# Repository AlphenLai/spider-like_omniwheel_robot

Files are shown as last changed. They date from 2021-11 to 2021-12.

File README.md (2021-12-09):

# spider-like_omniwheel_robot

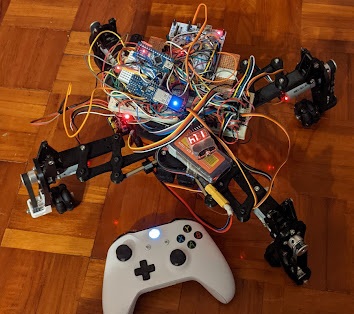
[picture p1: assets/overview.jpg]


This is a robot inspired by [Tachikoma](https://ghostintheshell.fandom.com/wiki/Tachikoma) from Ghost in the Shell. A robot with wheeled legs which allows it to switch between quadruped mode and vehicle mode.

This project was barely finished under a lot of compromise, due to series of inappropriate selection on software development platform and overthinking mechanical design. The robot is only capable in variable wheel angles by moving the position of its legs. Quadruped mode and other planned features are never implemented because of foreseeably  time-consuming efforts needed for completion.

## Hardware

### MCU

stm32f103rb nucleo

### Power Supply

MP1584EN DC-DC voltage regulator module (3A)

### Servo

MG995 servo (180 degree) x4

> note: 3A power supply is not enough to driver servo against any torque (eg: friction from ground). Continuing driving them will cause system blackout.

### Remote control

https://github.com/AlphenLai/arduino_nano_usb_host_shield

### Motor drivers

[TB6612FNG](https://www.sparkfun.com/datasheets/Robotics/TB6612FNG Breakout v11.zip) x2

### Motors 

25GA370 x4

280rpm, 12V

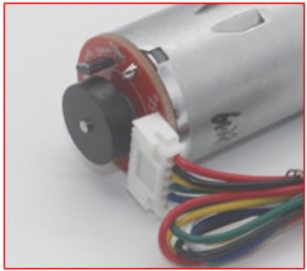
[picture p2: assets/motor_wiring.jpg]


| Colour | definition |
| --- | --- |
| Red | Motor + |
| Black  | Encoder -  |
| Yellow | Encoder A  |
| Green  | Encoder B  |
| Blue | Encoder +  |
| White  | Motor - |

### Wheel

1.5 inch omni wheel

### Chassis

[3D printed](./3D_printe_parts/)

Considered ease of program in omniwheel mode, and early planned "variable wheel angle", the legs are designed as concentric. This guarantee wheels being aligned to the centre as wherever the legs move, but also requires complicated mechanical design. This decision also scarified structural stability.

### Wiring



## Software

### OS

mbed-os. Unfortunately mbed-os is not designed for RTOS. It took a lot of efforts to implement the robot into the system.

| Module | Usage |
| --- | --- |
| config | Set pinout and global variables |
| controller | Handles controller signals (from serial) |
| encoder | Handles encoder feedbacks (signals proven to be delayed)  (discontinued) |
| extended_servo | Break servo movements by parts to create smooth transitions (discontinued) |
| hardware_io | Handles physical inputs such as buttons/potentiometer |
| **main** | Program entry point. Registers modules as threads |
| math_alg | Provide algorithm computation service (discontinued) |
| motion_control | Handles path following (discontinued) |
| motor_control  | Handles control signals to motor controller board |
| pid | Provide PID computation service (discontinued) |
| placeholder | Plain files for creating new module in mbed web compiler |
| serial | Handles serial traffic |
| servo_control  | Handles servo movements |
| usb_interface  | Handles usb interface in serial0/serial_pc. Receiver control signals from USB serial line. |

### Algorithm

#### Equation to drive a 4 wheels omniwheel robot



where 
R = radius of robot from body centre to wheel centre
r = radius of wheel
w = angular velocity of wheel
theta = body rotation (angle degree)
alpha = angle of wheel from centre of robot (assume the shaft points to centre of robot)
Vx = x axis velocity of robot
Vy = y axis velocity of robot
dot theta = angular velocity of robot (anti-clockwise)

To convert global frame to local frame (relative to robot body), multiple by the following matrix:



Compute the equation above will get the equation for each wheel:

**global frame**



**local frame**



For this robot, motors are ordered by body frame.

But their angles are assigned from 12 o'clock in clockwise due to the ease of following references in early stage.



## Demo

Watch the video (https://youtu.be/Zyg-uMiATHM)

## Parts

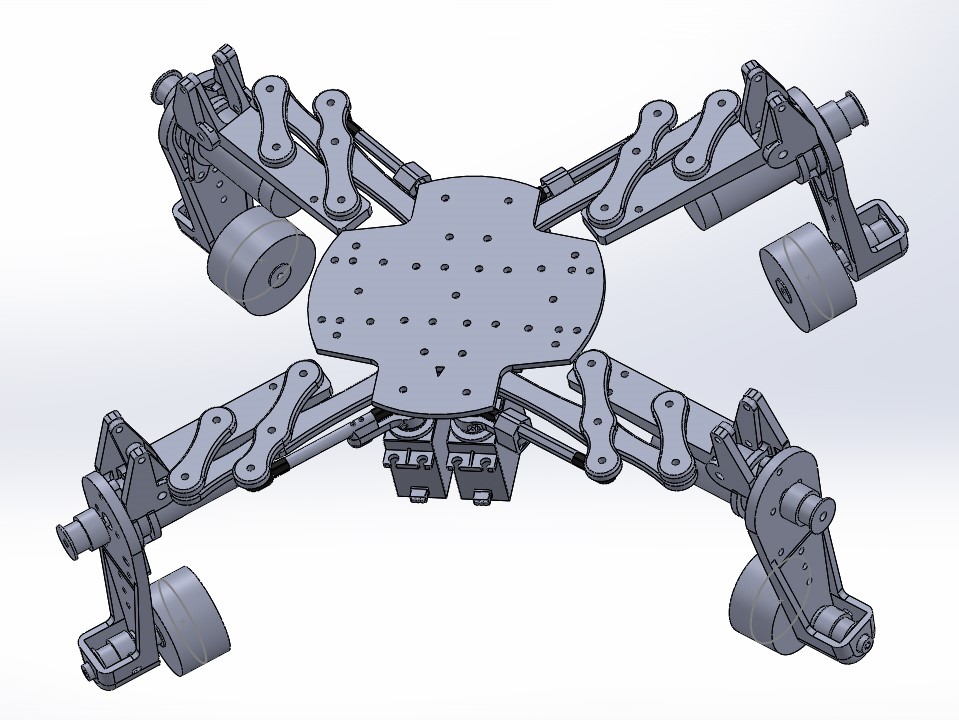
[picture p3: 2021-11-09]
3D_printed_parts/preview.JPG

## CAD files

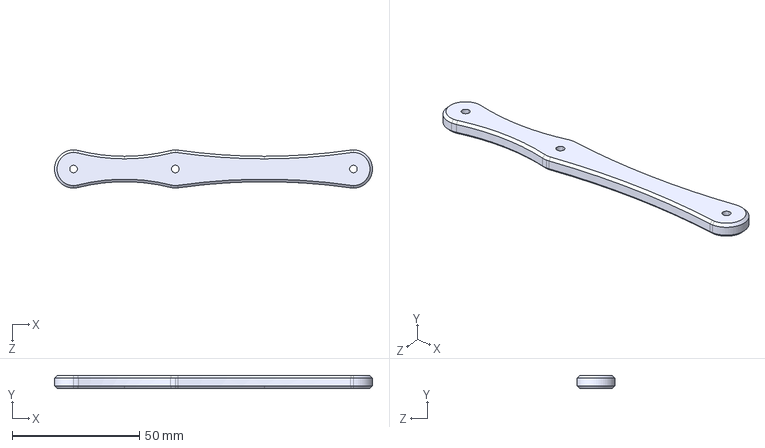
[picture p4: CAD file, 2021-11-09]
3D_printed_parts/x4_3dp_coxa_mainshaft.STEP
125.0 x 5.00 x 15.0 mm

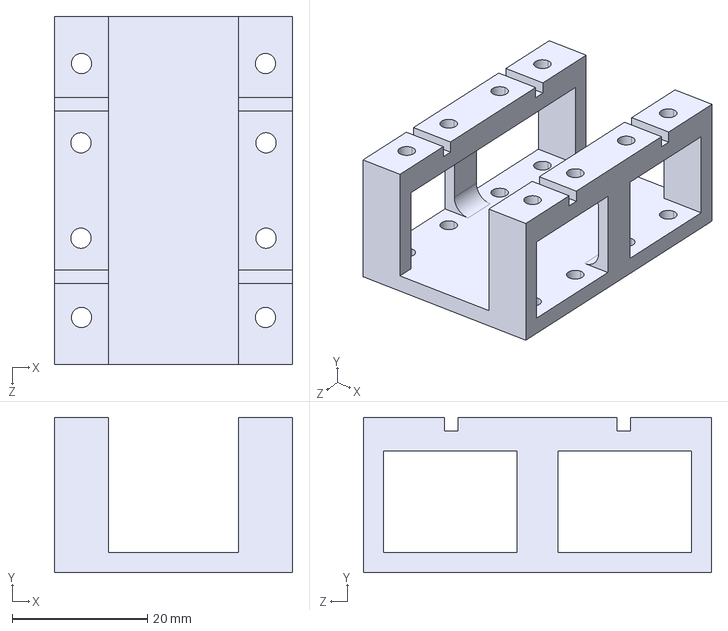
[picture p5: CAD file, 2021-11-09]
3D_printed_parts/x1_3DP_servo_mount_under_main.STEP
35.2 x 23.0 x 51.6 mm

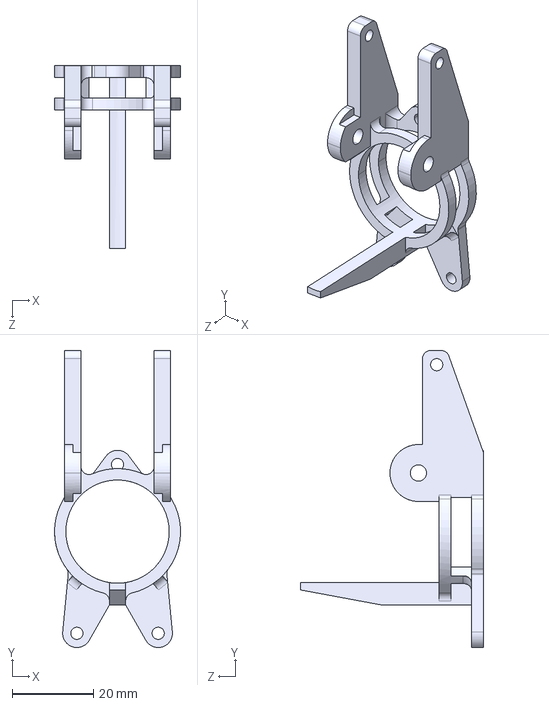
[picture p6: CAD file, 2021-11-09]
3D_printed_parts/x4_3dp_femur-leg.STEP
31.0 x 73.0 x 45.0 mm

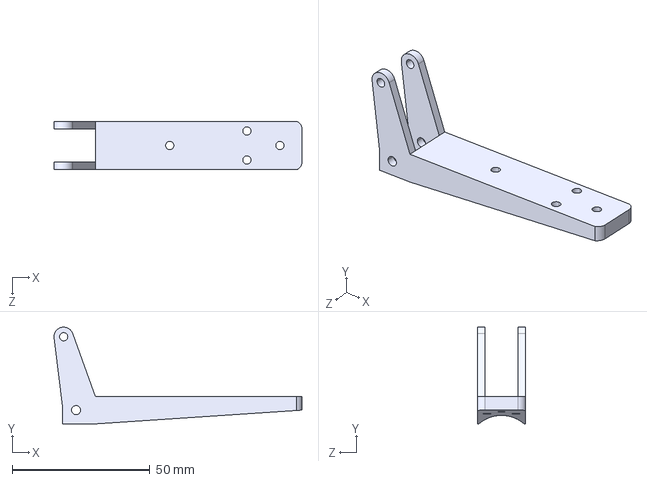
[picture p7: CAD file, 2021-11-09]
3D_printed_parts/x4_3dp_femur-fix.STEP
90.0 x 35.1 x 17.6 mm

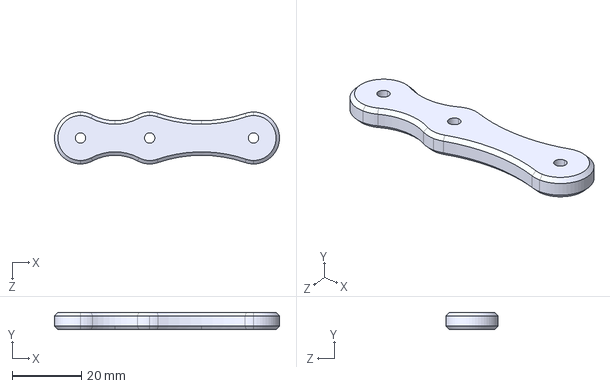
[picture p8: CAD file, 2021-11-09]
3D_printed_parts/x4_3dp_coxa_cross.STEP
65.0 x 5.00 x 15.0 mm

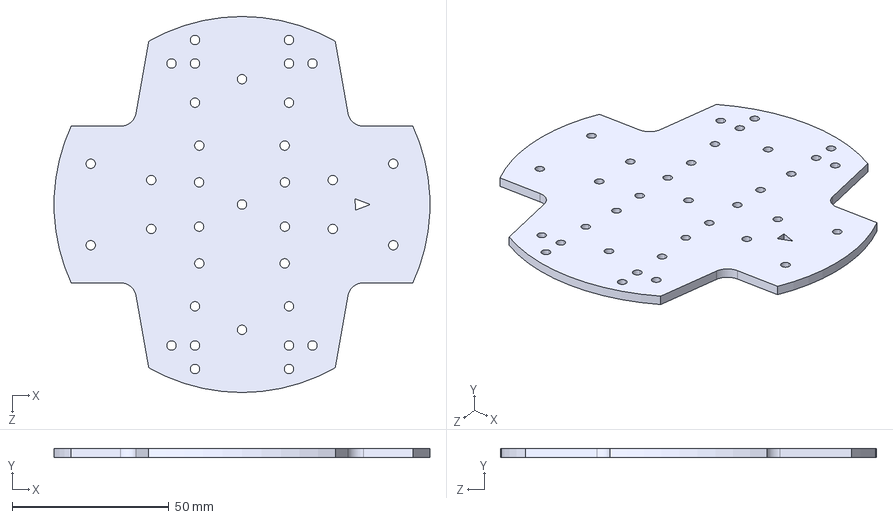
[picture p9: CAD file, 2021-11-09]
3D_printed_parts/x1_3dp_LC_body.STEP
119.9 x 3.00 x 120.0 mm

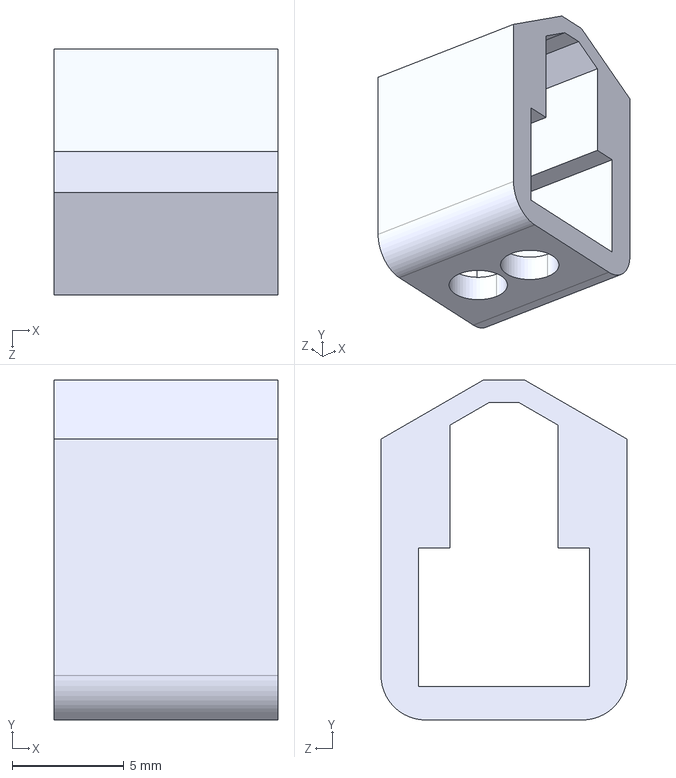
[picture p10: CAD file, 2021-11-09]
3D_printed_parts/x4_3dp_pillar_sheeve.STEP
10.0 x 15.2 x 11.0 mm

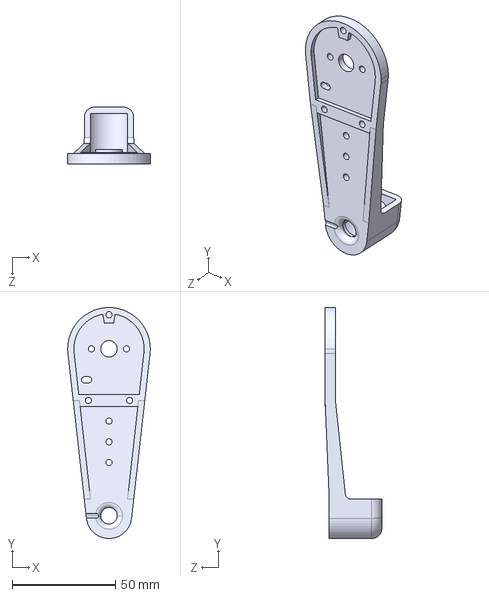
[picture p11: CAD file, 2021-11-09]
3D_printed_parts/x4_3dp_leg_proto_alt.STEP
40.0 x 111.8 x 27.5 mm

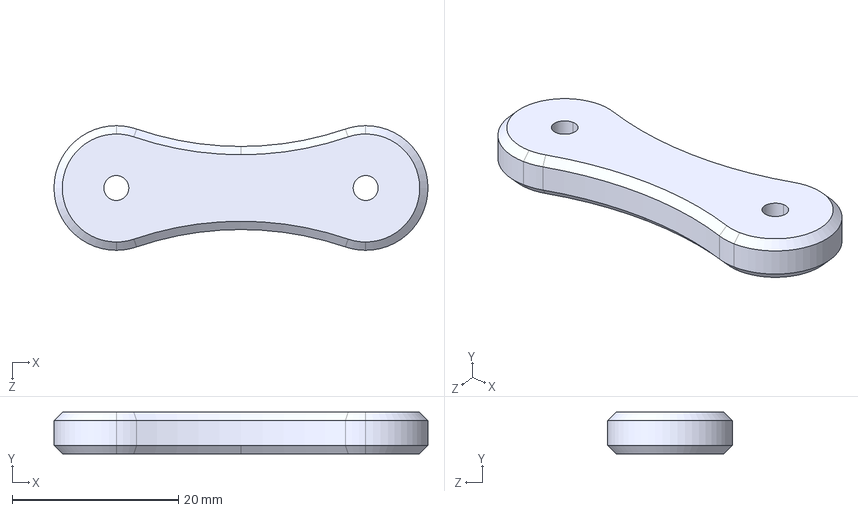
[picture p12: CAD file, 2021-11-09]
3D_printed_parts/x4_3dp_coxa_endshaft.STEP
45.0 x 5.00 x 15.0 mm

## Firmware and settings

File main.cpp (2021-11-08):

#include "mbed.h"
#include "config.h"
#include "serial.h"
#include "servo_control.h"
#include "hardware_io.h"
#include "motor_control.h"
#include "encoder.h"
#include "motion_control.h"
#include "usb_interface.h"
#include "controller.h"

#define USE_CONSOLE true

//place this line to io thread cpp later
DigitalOut debug_led(LD2);
extern Timer t;
extern RawSerial pc;

extern float sys_v_x;
extern float sys_v_y;
extern float sys_v_theta;

void led_thread()
{
    while (true) {
        debug_led = !debug_led;
        wait(1);
    }
}

int main()
{
    //Thread thread1(osPriorityNormal, 0.5 * 1024);   //0.5 * 1k stacks
    Thread thread2(osPriorityNormal, 1 * 1024);
    Thread thread3(osPriorityNormal, 0.5 * 1024);
    Thread thread4(osPriorityNormal, 1 * 1024);
    //Thread thread5(osPriorityNormal, 0.5 * 1024);
    //Thread thread6(osPriorityNormal, 1 * 1024);
    //Thread thread7(osPriorityNormal, 1 * 1024);
    Thread thread8(osPriorityNormal, 1 * 1024);
    Thread thread9(osPriorityNormal, 0.5 * 1024);
    
    pc.printf("\n\n=== Omniwheel Robot Test Platform ===\n\r");
    pc.printf("                            --Unit 00 v0 mod 1\n\n\r");
    t.start();
    
    //thread1.start(led_thread);
    thread2.start(servo_control);
    thread3.start(hardware_io);    
    thread4.start(motor_control);
    //thread5.start(encoder);
    //thread6.start(motion_control);
    //thread7.start(usb_interface);
    thread8.start(controller);
    thread9.start(serial);
    
    while(1)
    {
        wait(30);
        char buffer[50] = "running\n\r";
        pc_print(buffer);
        
        /*
        sys_v_x = 0.0;
        sys_v_y = 0.0;
        sys_v_theta = 3.0;
        wait(1);
        */
    }
}

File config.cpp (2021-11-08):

#include "config.h"
#include "mbed.h"
#include "extended_servo.h"
#include "motor_control.h"
#include "QEI.h"
#include "serial.h"

Timer t;

bool ready_to_start = false;

RawSerial pc(USBTX, USBRX, 57600); // tx, rx
RawSerial nano(S1TX, PB_7, 57600);

Serial_buffer pc_serial;
Serial_buffer nano_serial;

//put in a struct next version
const char *VAR_TABLE[] = {
    "ready_to_start",
    "motor1",
    "motor2",
    "motor3",
    "motor4",
    "m1_speed",
    "m2_speed",
    "m3_speed",
    "m4_speed",
    "sys_v_x = 0",
    "sys_v_y = 0.5",
    "sys_v_theta = 0",
    "sys_x = 0",
    "sys_y = 0",
    "sys_theta = 0",
    "m1_encoder",
    "m2_encoder",
    "m3_encoder",
    "m4_encoder"
};

uint8_t var_table_len = sizeof(VAR_TABLE);
uint8_t var_table_ele = sizeof(VAR_TABLE[0]);

//hw var
float wheel_r = 0.019;
float chassis_R = 0.1453;
float motor1_pos = 45.0 * pi/180.0;
float motor2_pos = 315.0 * pi/180.0;
float motor3_pos = 225.0 * pi/180.0;
#if MOTOR_NUMBER == 4
float motor4_pos = 135.0 * pi/180.0;
#endif

//servo var
#if USE_SERVO1 == true
Servo servo1(SERVO1_PIN);
Extended_servo servo1_handler;
#endif

float servo1_init = 45.0;
float servo1_angle = servo1_init;
float servo1_angle_range = 90;
float servo1_max = 0.875;
float servo1_min = 0.47;

#if USE_SERVO2 == true
Servo servo2(SERVO2_PIN);
Extended_servo servo2_handler;
#endif

float servo2_init = 45;
float servo2_angle = servo2_init;
float servo2_angle_range = 90;
float servo2_max = 0.84;
float servo2_min = 0.415;

#if USE_SERVO3 == true
Servo servo3(SERVO3_PIN);
Extended_servo servo3_handler;
#endif

float servo3_init = 45;
float servo3_angle = servo3_init;
float servo3_angle_range = 90;
float servo3_max = 0.85;
float servo3_min = 0.445;

#if USE_SERVO4 == true
Servo servo4(SERVO4_PIN);
Extended_servo servo4_handler;
#endif

float servo4_init = 45;
float servo4_angle = servo4_init;
float servo4_angle_range = 90;
float servo4_max = 0.845;
float servo4_min = 0.44;
//---

//motor var
float max_speed = 0.25;
float min_speed = -1.0;
float sys_speed = 1.0;                  //speed of the whole system

PwmOut m1_pwm_out(MOTOR1_PWM_PIN);
PwmOut m2_pwm_out(MOTOR2_PWM_PIN);
PwmOut m3_pwm_out(MOTOR3_PWM_PIN);
#if MOTOR_NUMBER == 4
PwmOut m4_pwm_out(MOTOR4_PWM_PIN);
#endif

DigitalOut m1_in1_out(MOTOR1_IN1_PIN);
DigitalOut m1_in2_out(MOTOR1_IN2_PIN);
DigitalOut m2_in1_out(MOTOR2_IN1_PIN);
DigitalOut m2_in2_out(MOTOR2_IN2_PIN);
DigitalOut m3_in1_out(MOTOR3_IN1_PIN);
DigitalOut m3_in2_out(MOTOR3_IN2_PIN);
#if MOTOR_NUMBER == 4
DigitalOut m4_in1_out(MOTOR4_IN1_PIN);
DigitalOut m4_in2_out(MOTOR4_IN2_PIN);
#endif

float m1_speed;                         //speed of individual motor in rad/s
float m2_speed;                         //speed of individual motor in rad/s
float m3_speed;                         //speed of individual motor in rad/s
#if MOTOR_NUMBER == 4
float m4_speed;                         //speed of individual motor in rad/s
#endif
Motor_controller motor1(MOTOR1_HW_INV);
Motor_controller motor2(MOTOR2_HW_INV);
Motor_controller motor3(MOTOR3_HW_INV);
#if MOTOR_NUMBER == 4
Motor_controller motor4(MOTOR4_HW_INV);
#endif
//---

//system motion
float sys_v_x = 0;
float sys_v_y = 0;
float sys_v_theta = 5;

float sys_x = 0;
float sys_y = 0;
float sys_theta = 0;
//---

//encoder var
QEI m1_encoder(MOTOR1_ENC_A, MOTOR1_ENC_B, NC, 624);
QEI m2_encoder(MOTOR2_ENC_A, MOTOR2_ENC_B, NC, 624);
QEI m3_encoder(MOTOR3_ENC_A, MOTOR3_ENC_B, NC, 624);
#if MOTOR_NUMBER == 4
QEI m4_encoder(MOTOR4_ENC_A, MOTOR4_ENC_B, NC, 624);
#endif

float m1_enc = 0;
float m2_enc = 0;
float m3_enc = 0;
#if MOTOR_NUMBER == 4
float m4_enc = 0;
#endif

//enc angular velocity
float cyc_pulse = 440.0;

float enc_v_x = 0;
float enc_v_y = 0;
float enc_v_theta = 0;

//enc odom
float enc_x = 0;
float enc_y = 0;
float enc_theta = 0;
//---

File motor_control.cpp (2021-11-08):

#include "motor_control.h"
#include "mbed.h"
#include "config.h"
#include "serial.h"
#include "math_alg.h"
#include "pid.h"

extern bool ready_to_start;
extern RawSerial pc;
extern Serial_buffer pc_serial;

extern float wheel_r;
extern float chassis_R;

extern float motor1_pos;
extern float motor2_pos;
extern float motor3_pos;
#if MOTOR_NUMBER == 4
extern float motor4_pos;
#endif

extern float max_speed;
extern float min_speed;
extern float sys_speed;

extern Motor_controller motor1;
extern Motor_controller motor2;
extern Motor_controller motor3;
#if MOTOR_NUMBER == 4
extern Motor_controller motor4;
#endif

extern PwmOut m1_pwm_out;
extern PwmOut m2_pwm_out;
extern PwmOut m3_pwm_out;
#if MOTOR_NUMBER == 4
extern PwmOut m4_pwm_out;
#endif

extern DigitalOut m1_in1_out;
extern DigitalOut m1_in2_out;
extern DigitalOut m2_in1_out;
extern DigitalOut m2_in2_out;
extern DigitalOut m3_in1_out;
extern DigitalOut m3_in2_out;
#if MOTOR_NUMBER == 4
extern DigitalOut m4_in1_out;
extern DigitalOut m4_in2_out;
#endif

extern float m1_speed;
extern float m2_speed;
extern float m3_speed;
#if MOTOR_NUMBER == 4
extern float m4_speed;
#endif

extern float sys_v_x;
extern float sys_v_y;
extern float sys_v_theta;

extern float sys_x;
extern float sys_y;
extern float sys_theta;
float max_rad = (chassis_R/wheel_r)*10;   //max possible angular speed of a wheel, assume sys_v_theta = 1 is maximum

Pid_sys enc_theta_offset(1, 1, 1, 0.05);
extern float enc_v_theta;

Motor_controller::Motor_controller(signed char wheel_inv)
{
    dir = wheel_inv;
    speed = 1.0;    //start up speed
}

float Motor_controller::get_speed()
{
    return speed;
}

void Motor_controller::set_speed(float spd)
{
    speed = dir * spd;
}

signed char Motor_controller::get_dir()
{
    return dir;     //whether the wheel is inverted
}
        
bool Motor_controller::dir_ctr(uint8_t pin)
{
    if (speed >= 0)          //+ve, 01
    {
        if (pin == 1)
            return 0;
        else if (pin == 2)
            return 1;
    } 
    else if (speed < 0)      //-ve, 10
    {
        if (pin == 1)
            return 1;
        else if (pin == 2)
            return 0;
    }
    return 0;
}

void motor_control()
{
    while(ready_to_start == false)
        wait(0.1);

    char buffer[50] = "motor service starts\n\r";
    pc_print(buffer);
    //printf("motor service starts\n\r");
    
    //m1_pwm_out.period_ms(MOTOR_PWM_PERIOD_MS);
    while(1)
    {
        //angle correction
        //float ref_offset = enc_theta_offset.get( (sys_v_theta - enc_v_theta)/enc_v_theta);
        //printf("\rsys_v : %f enc_v: %f dtheta: %f\n\r", sys_v_theta, enc_v_theta, ref_offset);
        
        #if MOTOR_NUMBER == 3
        //float temp0 = boundary(min_speed, motor4.get_speed(), max_speed);
        //printf("\rpwm4 out = %f\n", temp0);
        m1_speed = (-sin(sys_theta + motor1_pos) * cos(sys_theta) * sys_v_x + cos(sys_theta + motor1_pos) * cos(sys_theta) * sys_v_y + chassis_R * (sys_v_theta/*+ ref_offset*/))/wheel_r;
        motor1.set_speed(m1_speed/max_rad);
        m1_in1_out = motor1.dir_ctr(1);
        m1_in2_out = motor1.dir_ctr(2);
        //m1_pwm_out.write(boundary(min_speed, abs(motor1.get_speed()), max_speed));
        m1_pwm_out.write(abs(motor1.get_speed()));
        
        m2_speed = (-sin(sys_theta + motor2_pos) * cos(sys_theta) * sys_v_x + cos(sys_theta + motor2_pos) * cos(sys_theta) * sys_v_y + chassis_R * (sys_v_theta/* + ref_offset*/))/wheel_r;
        motor2.set_speed(m2_speed/max_rad);
        m2_in1_out = motor2.dir_ctr(1);
        m2_in2_out = motor2.dir_ctr(2);
        m2_pwm_out.write(abs(motor2.get_speed()));
        
        m3_speed = (-sin(sys_theta + motor3_pos) * cos(sys_theta) * sys_v_x + cos(sys_theta + motor3_pos) * cos(sys_theta) * sys_v_y + chassis_R * (sys_v_theta/* + ref_offset*/))/wheel_r;
        motor3.set_speed(m3_speed/max_rad);
        m3_in1_out = motor3.dir_ctr(1);
        m3_in2_out = motor3.dir_ctr(2);
        m3_pwm_out.write(abs(motor3.get_speed()));
        #endif
        
        #if MOTOR_NUMBER == 4
        //placeholder
        m1_speed = (-sin(sys_theta + motor1_pos) * cos(sys_theta) * sys_v_x + cos(sys_theta + motor1_pos) * cos(sys_theta) * sys_v_y + chassis_R * (sys_v_theta/*+ ref_offset*/))/wheel_r;
        motor1.set_speed(m1_speed/max_rad);
        m1_in1_out = motor1.dir_ctr(1);
        m1_in2_out = motor1.dir_ctr(2);
        m1_pwm_out.write(abs(motor1.get_speed()));
        
        m2_speed = (-sin(sys_theta + motor2_pos) * cos(sys_theta) * sys_v_x + cos(sys_theta + motor2_pos) * cos(sys_theta) * sys_v_y + chassis_R * (sys_v_theta/* + ref_offset*/))/wheel_r;
        motor2.set_speed(m2_speed/max_rad);
        m2_in1_out = motor2.dir_ctr(1);
        m2_in2_out = motor2.dir_ctr(2);
        m2_pwm_out.write(abs(motor2.get_speed()));
        
        m3_speed = (-sin(sys_theta + motor3_pos) * cos(sys_theta) * sys_v_x + cos(sys_theta + motor3_pos) * cos(sys_theta) * sys_v_y + chassis_R * (sys_v_theta/* + ref_offset*/))/wheel_r;
        motor3.set_speed(m3_speed/max_rad);
        m3_in1_out = motor3.dir_ctr(1);
        m3_in2_out = motor3.dir_ctr(2);
        m3_pwm_out.write(abs(motor3.get_speed()));
        
        m4_speed = (-sin(sys_theta + motor4_pos) * cos(sys_theta) * sys_v_x + cos(sys_theta + motor4_pos) * cos(sys_theta) * sys_v_y + chassis_R * (sys_v_theta/* + ref_offset*/))/wheel_r;
        motor4.set_speed(m4_speed/max_rad);
        m4_in1_out = motor4.dir_ctr(1);
        m4_in2_out = motor4.dir_ctr(2);
        m4_pwm_out.write(abs(motor4.get_speed()));
        #endif
        
        //printf("\rout- m1 : %.3f | m2: %.3f | m3 : %.3f\n\r", motor1.get_speed(), motor2.get_speed(), motor3.get_speed());
        //printf("\r%.3f | %.3f | %.3f | %.3f\n\r", motor1.get_speed(), motor2.get_speed(), motor3.get_speed(), motor4.get_speed());
        while(ready_to_start == false)
        {
            m1_pwm_out.write(0.0);
            m2_pwm_out.write(0.0);
            m3_pwm_out.write(0.0);
            #if MOTOR_NUMBER == 4
            m4_pwm_out.write(0.0);
            #endif
            wait(0.1);
        }
    }
}

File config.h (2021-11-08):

#ifndef Config_H_
#define Config_H_

#define pi                  3.14159265359

#define USE_SERVO1          true
#define SERVO1_PULSE_WIDTH  0.001     //0.00125 for white servo, 0.001 for MG995
#define SERVO1_HW_RANGE     180

#define USE_SERVO2          true
#define SERVO2_PULSE_WIDTH  0.001
#define SERVO2_HW_RANGE     180

#define USE_SERVO3          true
#define SERVO3_PULSE_WIDTH  0.001
#define SERVO3_HW_RANGE     180

#define USE_SERVO4          true
#define SERVO4_PULSE_WIDTH  0.001
#define SERVO4_HW_RANGE     180

#define USE_ADC_ROTARY      false
#define ADC_ROTARY_FUNC     SERVO1_CONT
#define ADC_ROTARY_MAX      0.77
#define ADC_ROTARY_MIN      0.4

#define MOTOR_NUMBER        4
#define MOTOR_PWM_PERIOD_MS 10

#define ENC_CYCLE_SIZE      11

#define MOTOR1_HW_INV       1
#define MOTOR2_HW_INV       1
#define MOTOR3_HW_INV       1
#define MOTOR4_HW_INV       1

// ***Define all pin assignments and setup in this file***
#define LD2                 LED1

//PWM1/1-4
#define SERVO1_PIN          PA_10
#define SERVO2_PIN          PA_9
#define SERVO3_PIN          PA_8
#define SERVO4_PIN          PA_11

#define ROTARY_PIN_A        PC_1
#define ROTARY_PIN_B        PC_0
//#define ROTARY_PIN_SW       PB_0

#define ON_BRD_BTN          PC_13

#define ADC_PIN_1           PA_0

//PWM3/1-4
#define MOTOR1_PWM_PIN      PC_8
#define MOTOR1_IN1_PIN      PB_1
#define MOTOR1_IN2_PIN      PB_15
#define MOTOR1_ENC_A        PB_2
#define MOTOR1_ENC_B        PC_3

#define MOTOR2_PWM_PIN      PC_9
#define MOTOR2_IN1_PIN      PB_14
#define MOTOR2_IN2_PIN      PB_13
#define MOTOR2_ENC_A        PC_4
#define MOTOR2_ENC_B        PC_5

#define MOTOR3_PWM_PIN      PC_6
#define MOTOR3_IN1_PIN      PA_14
#define MOTOR3_IN2_PIN      PC_12
#define MOTOR3_ENC_A        PA_6
#define MOTOR3_ENC_B        PA_7

#define MOTOR4_PWM_PIN      PC_7
#define MOTOR4_IN1_PIN      PA_4
#define MOTOR4_IN2_PIN      PB_0
#define MOTOR4_ENC_A        PB_12
#define MOTOR4_ENC_B        PA_13

#define S1TX                PB_6
#define S1RX                PB_7
#define S2TX                PA_2
#define S2RX                PA_3
#define S3TX                PC_10
#define S3RX                PC_11


//4servo    pwmout
//4motor    pwmout
//?reserve more pwmouts
//1lcd?     i2c
//idial     analog
//?comm     serials(as much as it can)
//1sd card  spi

/*  Design pinout of this board
serial:
SERIAL1_TX  PB_6    D10
SERIAL1_RX  PB_7    
SERIAL2_TX  PA_2    D1
SERIAL2_RX  PA_3    D0
SERIAL3_TX  PC_10
SERIAL3_RX  PC_11

i2c:
I2C1_SCL    PB_8    D15
I2C1_SDA    PB_9    D14
I2C2_SCL    PB_10   D6
I2C2_SDA    PB_11

spi:
SPI1_MISO   PB_4    D5
SPI1_MOSI   PB_5    D4
SPI1_SCK    PB_3    D3
SPI1_NSS    PA_15

pwm:
go test signals 
PC_9 and PB_1
PB_15 and PA_10

io:
onboard_btn PC_13
onboard_led PA_5

*/

/*  Quick lookup table for nucleo pins conversion
PA_0    A0
PA_1    A1  PWM2/2
PA_2    D1  PWM2/3      S2_TX       (ANALOG)
PA_3    D0  PWM2/4      S2_RX       (ANALOG)
PA_4    A2              SPI1_NSS
PA_5    D13 LED1/LD2    SPI1_SCK    (ANALOG)
PA_6    D12 PWM3/1      SPI1_MISO   (ANALOG)
PA_7    D11 PWM3/2      SPI1_MOSI   (ANALOG)
PA_9    D8  PWM1/2?     S1_TX
PA_8    D7  PWM1/1?
PA_9    D8  PWM1/2      S1_TX
PA_10   D2  PWM1/3      S1_RX
PA_11       PWM1/4
PA_12
PA_13
PA_14
PA_15       PWM2/1      SPI1_NSS

PB_0    A3  PWM3/3
PB_1        PWM3/4                  (ANALOG)
PB_2
PB_3    D3  PWM2/2      SPI1_SCK
PB_4    D5  PWM3/1      SPI1_MISO
PB_5    D4  PWM3/2      SPI1_MOSI
PB_6    D10 PWMx/y?     S1_TX       CS
PB_7                    S1_RX
PB_8    D15                         I2C1_SCL
PB_9    D14                         I2C1_SDA
PB_10   D6  PWM2/3      S3_TX       I2C2_SCL
PB_11       PWM2/4?     S3_RX       I2C2_SDA
PB_12                   SPI2_NSS
PB_13       PWM1/1N     SPI2_SCK
PB_14       PWM1/2N     SPI2_MISO
PB_15       PWM1/3N     SPI2_MOSI

PC_0    A5
PC_1    A4
PC_4                                (ANALOG)
PC_5                                (ANALOG)
PC_6        PWM3/1
PC_7    D9  PWM3/2
PC_8        PWM3/3
PC_9        PWM3/4
PC_10                   S3_TX
PC_12
PC_13       USER_BUTTON

Alternate pins (Px_y_ALTz)
*/


// Parameters

#endif

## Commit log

2021-11-08 Update README.md
    Additional information on servo
2021-11-09 Upload 3D parts
    [x1_3DP_servo_mount_under_main.STEP, x1_3dp_LC_body.STEP, x1_3dp_wheel_shaft_aio.STEP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]
2021-11-09 Correct number of parts
    [x1_3dp_wheel_shaft_aio.STEP, x4_3dp_coxa_cross.STEP, x4_3dp_coxa_endshaft.STEP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]
